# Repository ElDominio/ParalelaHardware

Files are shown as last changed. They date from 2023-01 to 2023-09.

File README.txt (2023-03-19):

4-channel slim ECU with APM32F407VGT6, designed to use RusEFI

4 injection channel
4 ignition channels
additional outputs for boost/fuel pumps/idle/etc
onboard CAN
Hall or external VR conditioner
USB-C connection

No official firmware for this board (for now)

CPU pinout inside "Reference" folder

How to open EasyEDA Project File：

At editor, open the document via: Top menu - File - Open - EasyEDA... , and select the json file, then open it at the editor, you can save it into a project.

如何使用：

打开编辑器，通过：顶部菜单 - 文件 - 打开 - 立创EDA... ，选择 json 文件打开在编辑器，你可以保存文档进工程里面。

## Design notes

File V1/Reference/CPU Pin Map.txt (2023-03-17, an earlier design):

4X4 ECU CPU Pin Map
-------------------

( APM32F407VGT6 )

Ignition 1 >> PA8
Ignition 2 >> PC9
Ignition 3 >> PA10
Ignition 4 >> PC8

Injector 1 >> PE0
Injector 2 >> PE6
Injector 3 >> PA3
Injector 4 >> PA5

IDLE       >> PC5
BOOST      >> PA7
NOS        >> PA6
FAN        >> PC13
FUEL PUMP  >> PC14
TACH       >> PC15

TPS        >> PA0
MAP        >> PA1
CLT        >> PA2
O2         >> PC3
IAT        >> PC2
VBAT       >> PC1

FLEX       >> PE1
CLUTCH     >> PE2

CRANK      >> PE3
CAM        >> PE5

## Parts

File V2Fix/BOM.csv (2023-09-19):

ID | Name | Designator | Footprint | Quantity | Manufacturer Part | Manufacturer | Supplier | Supplier Part | Price
1 | 100nF | C12,C1,C52,C3,C5,C18,C20,C24,C27,C29,C30,C32,C36,C39,C40,C42,C44,C51,C55,C56,C57,C58,C59,C60 | C0402 | 24 | CL05B104KB54PNC | Samsung Electro-Mechanics | LCSC | C307331 | 0.007
2 | 1nF | C34,C35,C14,C16,C17,C22,C23 | C0603 | 7 | CL10B102KB8NNNC | SAMSUNG(三星) | LCSC | C1588 | 0.003
3 | 2.49kΩ | R79 | R1206 | 1 | PTFR1206B2K49P9 | ResistorToday | LCSC | C351475 | 0.222
4 | B340A | D23 | SMA_L4.3-W2.6-LS5.2-RD | 1 | B340A | MDD | LCSC | C64982 | 0.038
5 | 2.4kΩ | R12,R16 | R0402 | 2 | 0402WGF2401TCE | UNI-ROYAL(厚声) | LCSC | C25882 | 0.001
6 | FC-F1005HRK-620H5 | LED1,LED3,LED8,LED9,LED10,LED11 | LED0402-RD | 6 | NCD0402R1 | 国星光电 | LCSC | C130719 | 0.036
7 | SZYY0402B | LED18,LED12,LED13,LED14,LED15 | LED0402-RD_BLUE | 5 | SZYY0402B | yongyu(永裕光电) | LCSC | C434447 | 0.016
8 | 1kΩ | R90,R82,R73,R74,R80,R81,R89 | R0402 | 7 | 0402WGF1001TCE | UNI-ROYAL(厚声) | LCSC | C11702 | 0.001
9 | Header-Male-2.54_2x3 | J1 | HDR-TH_6P-P2.54-V-M-R2-C3-S2.54-1 | 1 | 2.54-2*3P针 | BOOMELE(博穆精密) | LCSC | C65114 | 0.031
10 | 100Ω | L1 | L0805 | 1 | GZ2012D101TF | Sunlord | LCSC | C1015 | 0.009
11 | 10kΩ | RN1 | RES-ARRAY-SMD_0603-8P-L3.2-W1.6-BL | 1 | RC-ML08W103JT | FH | LCSC | C69593 | 0.004
12 | 1uF | C2,C4,C6,C19,C21,C25,C31,C33,C37 | C0402 | 9 | CL05A105KA5NQNC | SAMSUNG | LCSC | C52923 | 0.004
13 | B130-13-F | D1 | SMA_L4.3-W2.6-LS5.2-RD | 1 | B130-13-F | DIODES | LCSC | C134423 | 0.076
14 | SMBJ15CA | D2 | SMB_L4.6-W3.6-LS5.3-BI | 1 | SMBJ15CA | MDD | LCSC | C113989 | 0.046
15 | SMAJ33CA | D3,D4,D5,D11,D12,D13,D14 | SMA_L4.4-W2.6-LS5.0-BI | 7 | SMAJ33CA | MDD | LCSC | C115251 | 0.036
16 | NCE6020AK | Q1,Q6,Q7,Q4,Q5 | TO-252-2_L6.6-W6.1-P4.57-LS10.1-TL-CW | 5 | NCE6020AK | NCE(无锡新洁能) | LCSC | C108639 | 0.136
17 | MCP1416T-E/OT | U4,U5,U6,U8,U9,U13,U14 | SOT-23-5_L3.0-W1.7-P0.95-LS2.8-BL | 7 | MCP1416T-E/OT | MICROCHIP(美国微芯) | LCSC | C83775 | 0.441
18 | USB-TYPE-C-018 | USB1 | USB-C_SMD-TYPE-C-31-M-12 | 1 | USB-TYPE-C-018 | DEALON(德艺隆) | LCSC | C2927038 | 0.052
19 | SZYY0402G | LED16,LED2,LED4,LED5,LED6,LED7 | LED0402-R-RD_GREEN | 6 | SZYY0402G | yongyu(永裕光电) | LCSC | C434446 | 0.016
20 | 100uF | C7 | CAP-SMD_BD6.3-L6.6-W6.6-LS7.4-FD | 1 | RVT100UF35V67RV0034 | KNSCHA(科尼盛) | LCSC | C2836442 | 0.032
21 | 100nF | C8,C9 | C0603 | 2 | CC0603KRX7R9BB104 | YAGEO | LCSC | C14663 | 0.002
22 | 100uF | C10 | CAP-SMD_BD8.0-L8.3-W8.3-RD | 1 | VEJ101M1HTR-0810 | lelon(立隆) | LCSC | C176665 | 0.094
23 | 10uF | C11,C13 | CAP-SMD_L3.2-W1.6-RD-C7171 | 2 | TAJA106K016RNJ | AVX | LCSC | C7171 | 0.094
24 | 1nF | C15,C45,C46,C49,C50 | C0402 | 5 | 0402B102K500NT | FH | LCSC | C1523 | 0.001
25 | 470pF | C47,C48 | C0402 | 2 | 0402B471K500NT | FH | LCSC | C1537 | 0.001
26 | 2.2uF | C53,C64 | C0402 | 2 | CL05A225MQ5NSNC | SAMSUNG | LCSC | C12530 | 0.003
27 | 20pF | C62,C63 | C0402 | 2 | 0402CG200J500NT | FH(风华) | LCSC | C1554 | 0.002
28 | 5557R-2*3P | CN1,CN2 | CONN-TH_5557R-2X3P | 2 | W-5557R06P-0000 | Ckmtw(灿科盟) | LCSC | C124425 | 0.225
29 | 5557R-2*10P | CN3 | CONN-TH_5557R-2-10P | 1 | 5557R-2*10P | Ckmtw | LCSC | C169048 | 0.544
30 | 1N4148WS T4 | D6,D7,D8,D9,D10,D18,D19,D20,D21,D22 | SOD-323_L1.8-W1.3-LS2.5-RD | 10 | 1N4148WS | CJ(江苏长电/长晶) | LCSC | C2128 | 0.01
31 | BAV70 | D15,D16,D17 | SOT-23_L2.9-W1.3-P1.90-LS2.4-BR | 3 | BAV70 | LGE(鲁光) | LCSC | C402233 | 0.014
32 | NCE6005AR | Q2,Q3 | SOT-223_L6.5-W3.5-P2.30-LS7.0-BR | 2 | NCE6005AR | NCE(无锡新洁能) | LCSC | C189606 | 0.172
33 | CJ2310 | Q8,Q9,Q10 | SOT-23-3_L2.9-W1.6-P1.90-LS2.8-BR | 3 | CJ2310 | CJ | LCSC | C75882 | 0.047
34 | 1kΩ | R1 | R1206 | 1 | 1206W4F1001T5E | UNI-ROYAL(厚声) | LCSC | C4410 | 0.003
35 | 27Ω | R2,R6,R7,R25,R27,R47,R49 | R0603 | 7 | 0603WAF270JT5E | UNI-ROYAL(厚声) | LCSC | C25190 | 0.001
36 | 1kΩ | R3,R4,R5,R21,R23,R26,R28,R29,R36,R43,R45,R48,R50,R51,R58,R83 | R0402 | 16 | 0402WGF1001TCE | UniOhm | LCSC | C11702 | 0.001
37 | 10kΩ | R8,R14,R15,R31,R33,R53,R55 | R0603 | 7 | 0603WAF1002T5E | UNI-ROYAL(厚声) | LCSC | C25804 | 0.001
38 | 10kΩ | R9,R10,R11,R22,R32,R34,R35,R44,R54,R56,R57,R66,R85,R86 | R0402 | 14 | 0402WGF1002TCE | UniOhm | LCSC | C25744 | 0.001
39 | 1.5kΩ | R13,R17,R18,R19,R20,R62,R63,R64,R65,R77 | R0402 | 10 | 0402WGF1501TCE | UNI-ROYAL(厚声) | LCSC | C25867 | 0.001
40 | 10Ω | R24,R30,R46,R52 | R1206 | 4 | AS0606J0100T5E | UNI-ROYAL(Uniroyal Elec) | LCSC | C966096 | 0.032
41 | 10kΩ | R37,R38,R39,R40,R59,R60,R68,R69,R75,R76 | R0402 | 10 | AR02BTC1002 | Viking Tech | LCSC | C317926 | 0.03
42 | 20kΩ | R41,R42,R61,R71,R78 | R0603 | 5 | AR03BTCX2002 | Viking(光颉) | LCSC | C319766 | 0.032
43 | 2.7kΩ | R67,R72 | R0603 | 2 | RT0603BRD072K7L | YAGEO(国巨) | LCSC | C705760 | 0.026
44 | 120Ω | R70 | R0805 | 1 | 0805W8F1200T5E | UniOhm | LCSC | C17437 | 0.002
45 | 100Ω | R84 | R0402 | 1 | 0402WGF1000TCE | UNI-ROYAL(厚声) | LCSC | C25076 | 0.001
46 | L78M05CDT-TR | U1 | TO-252-3_L6.5-W5.8-P4.58-BL | 1 | L78M05CDT-TR | ST(意法半导体) | LCSC | C55509 | 0.155
47 | SPX3819M5-L-3-3/TR | U2 | SOT-23-5_L3.0-W1.7-P0.95-LS2.8-BR | 1 | SPX3819M5-L-3-3/TR | EXAR | LCSC | C9055 | 0.149
48 | ULN2001D | U3 | SOP-8_L4.9-W3.9-P1.27-LS6.0-TL | 1 | ULN2001D | LANKE(兰科) | LCSC | C2828554 | 0.075
49 | TC4424AVOA713 | U7,U12 | SOIC-8_L4.9-W3.9-P1.27-LS6.0-BL | 2 | TC4424AVOA713 | MICROCHIP(美国微芯) | LCSC | C44150 | 0.767
50 | MCP6004T-I/ST | U10 | TSSOP-14_L5.0-W4.4-P0.65-LS6.4-BL | 1 | MCP6004T-I/ST | MICROCHIP(美国微芯) | LCSC | C50282 | 0.638
51 | MCP6001T-I/OT | U11 | SOT-23-5_L3.0-W1.7-P0.95-LS2.8-BR | 1 | MCP6001T-I/OT | MICROCHIP(美国微芯) | LCSC | C116490 | 0.289
52 | SN65HVD230DR | U15 | SOIC-8_L4.9-W3.9-P1.27-LS6.0-BL | 1 | SN65HVD230DR | TI | LCSC | C12084 | 0.959
53 | 8 MHz | X1 | OSC-SMD_L5.0-W3.2 | 1 | NX5032GA-8MHZ(STD-CSK-7) | Nihon Dempa Kogyo | LCSC | C156253 | 0.273
54 | 1uF | C65 | C0805 | 1 | CL21B105KBFNNNE | SAMSUNG(三星) | LCSC | C28323 | 0.009
55 | 10kΩ | R87 | R0805 | 1 | ARG05BTC1002 | Viking(光颉) | LCSC | C406725 | 0.025
56 | 82kΩ | R88 | R0805 | 1 | PTFR0805B82K0N9 | RESI(开步睿思） | LCSC | C351545 | 0.151
57 | SRV05-4-P-T7 | TV2 | SOT-23-6_L2.9-W1.6-P0.95-LS2.8-BR | 1 | SRV05-4-P-T7 | PROTEK | LCSC | C85364 | 0.176
58 | APM32F407VGT6 | U16 | LQFP-100_L14.0-W14.0-P0.50-LS16.0-BL | 1 | APM32F407VGT6 | Geehy(珠海极海) | LCSC | C2990873 | 4.434
59 | TZ-P2-0402GTIA1-0.45T | LED17 | LED0402-RD | 1 | TZ-P2-0402GTIA1-0.45T | TUOZHAN(拓展光电) | LCSC | C688877 | 0.011

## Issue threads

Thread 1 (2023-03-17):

separate versioned output from sources

rusefillc, 2023-03-17:
current file structure is a naive mess

please be like proteus - explicit separate folder for each revision of outputs like https://github.com/mck1117/proteus/tree/master/export

ElDominio, 2023-03-19:
Solved by 720e451

Closed 2023-03-19.

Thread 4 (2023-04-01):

programming header: reset less important than GND

rusefillc, 2023-04-01:
if you have only three pins GND should be one of those. Reset is kind of optional less imporant

ElDominio, 2023-04-16:
Fixed by b19c86d

Closed 2023-04-16.

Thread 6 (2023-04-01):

arm chip should be powered by USB

rusefillc, 2023-04-01:
if you hook USB you should have 3.3 on the chip and happy chip right?

ElDominio, 2023-04-02:
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

Adding a solder bridge here produces a chip that is happy to wake on USB connection

ElDominio, 2023-04-16:
Fixed by b19c86d

Closed 2023-04-16.

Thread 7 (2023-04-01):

LEDs are WAY too bright, use other color

ElDominio, 2023-04-01:
5v and 12v LEDs are incredibly bright

ElDominio, 2023-04-16:
Fixed by b19c86d

Closed 2023-04-16.

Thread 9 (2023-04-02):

c'mon no blue LED to show life?

rusefillc, 2023-04-02:
Please consider a blue "firmware is alive" LED

ElDominio, 2023-04-02:
to what pin does it get connected to?

ElDominio, 2023-04-16:
Fixed by b19c86d

Closed 2023-04-16.

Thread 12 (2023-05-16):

PC14 does not work, all other outputs do

ElDominio, 2023-05-16:
As stated, PC14 seems to do nothing. Is this pin different on APM32?

rusefillc, 2023-05-16:
"google PC14 stm32" to see if that's one of the special magic pins

looks like it's a pin for low speed oscillator?

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

This indicates that custom binary would be needed which is major effort. Would it be possible to adjust hardware and use a less magical stm32 pin?

ElDominio, 2023-09-19:
Changed pin

Closed 2023-09-19.

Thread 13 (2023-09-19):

only Some APM32 Paralelas report "Device Descriptor Request Failed" on USB, processor seems alive?

ElDominio, 2023-09-19:
Some Paralelas after flashing f407-discovery seem to have USB comms die, but still talk fine with STLink, and flash leds as if everything is ok. Satanic possesion? Probably due to Geehy not being STM and incompatibilities from this

rusefillc, 2023-09-25:
https://github.com/ElDominio/ParalelaHardware/blob/main/V2Fix/Schematic.pdf

ElDominio, 2023-09-30:
Most of them flash fine, connect to tunerstudio, and after you disconnect and reconnect they never come back to life through usb, even though processor seems to be alive and well

rusefillc, 2023-10-07:
@ElDominio what oscillator frequency is mounter? 8mhz? 12mhz? else?

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

rusefillc, 2023-10-07:
```"8 MHz"	"X1"	"OSC-SMD_L5.0-W3.2"	"1"	"NX5032GA-8MHZ(STD-CSK-7)"	"Nihon Dempa Kogyo"```

ElDominio, 2023-10-07:
Where is that? in STM32cube? Or in Device Manager?

rusefillc, 2023-10-07:
> Where is that? in STM32cube? Or in Device Manager? I don't even know what a "mounter" is

that's eclipse debugging session

ElDominio, 2023-10-07:
> Most of them flash fine, connect to tunerstudio, and after you disconnect and reconnect they never come back to life through usb, even though processor seems to be alive and well

Just quoting this because of oddness.
USB comms dies, but everything else is still alive, you can flash firmware as many times as you want but it will still be broken

ElDominio, 2023-10-17:
@rusefillc not due to processor, same happens on OG STM32 boards. Still alive through DFU

ElDominio, 2023-10-17:
weirder: they started talking through USB again? with no intervention from my part?

rusefillc, 2023-10-17:
smells like firmware issue

ElDominio, 2023-10-19:
Another fun fact:

I got another batch of STM32 Paralelas, have only tested 3 but I have loaded firmware+tune and they all seem alive and well, even with multiple USB connect/disconnects. This is pointing more to a specific hardware+firmware issue concerning APM32. Will have more tests coming in the coming weeks.

@rusefillc  you need 3 STM, and you will ship 1x APM + 1 STM Paralela to Ukraine correct?

rusefillc, 2023-10-19:
@ElDominio I am mostly interested in BROKEN stm32

please do NOT ship any stm32 of the "good" batch

ElDominio, 2023-10-19:
At the current time, ALL STM32 Paralelas are working fine. Two had a hiccup yesterday but seem to be back to life with no further errors. Next one that locks up I will put in a box for @rusefillc

ElDominio, 2023-10-29:
This seems to be very APM-specific. Up until now _ALL_ STM32's have not suffered this for more than one or two restarts, after which it does not come back.

ElDominio, 2024-02-23:
This is due to using APM32 chips. Zero STM chips have had this issue. If not useful, will close

ElDominio, 2024-04-06:
Not useful, will close

Closed 2024-04-06.

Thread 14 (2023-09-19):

Paralela magic smoke report

ElDominio, 2023-09-19:
Users were working on alternator with engine on, seem to have overvolted by a large degree resulting in D2 diode exploding

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

ElDominio, 2023-10-29:
Owner used battery booster in engine start and fed >16v. Diode was overvolt protection diode, replaced diode and is still alive

Closed 2023-10-29.

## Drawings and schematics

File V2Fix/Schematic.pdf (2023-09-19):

A | A

1

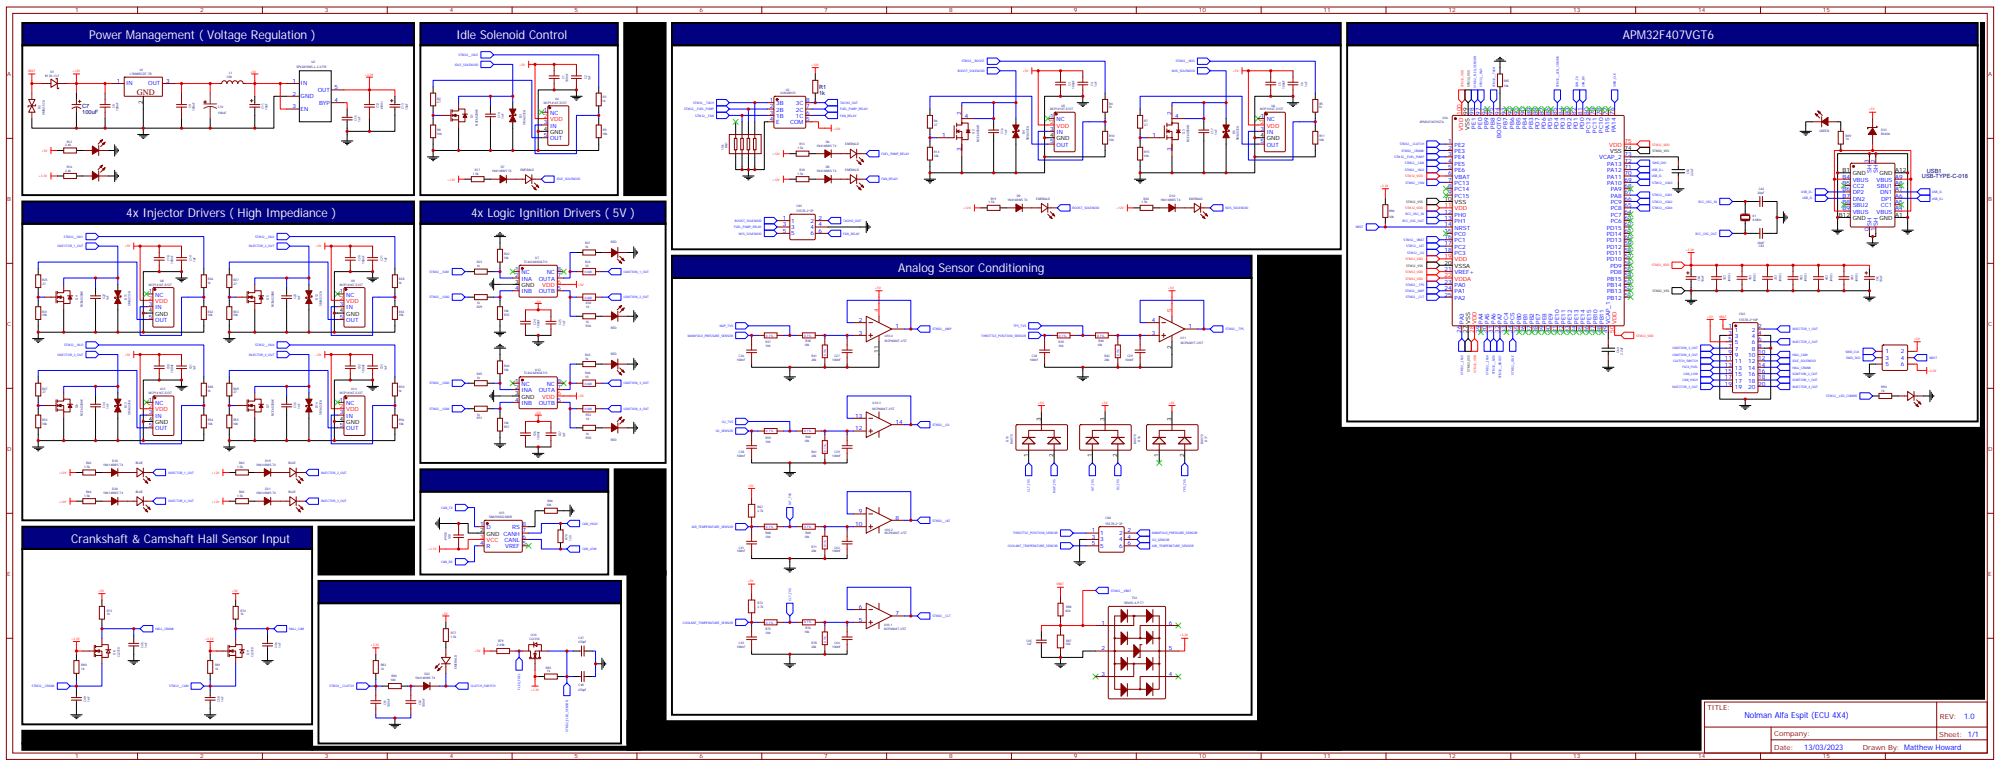
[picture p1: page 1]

Power Management ( Voltage Regulation )

4x Injector Drivers ( High Impediance )

Drawn By: Matthew Howard

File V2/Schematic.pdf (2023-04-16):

A | A

1

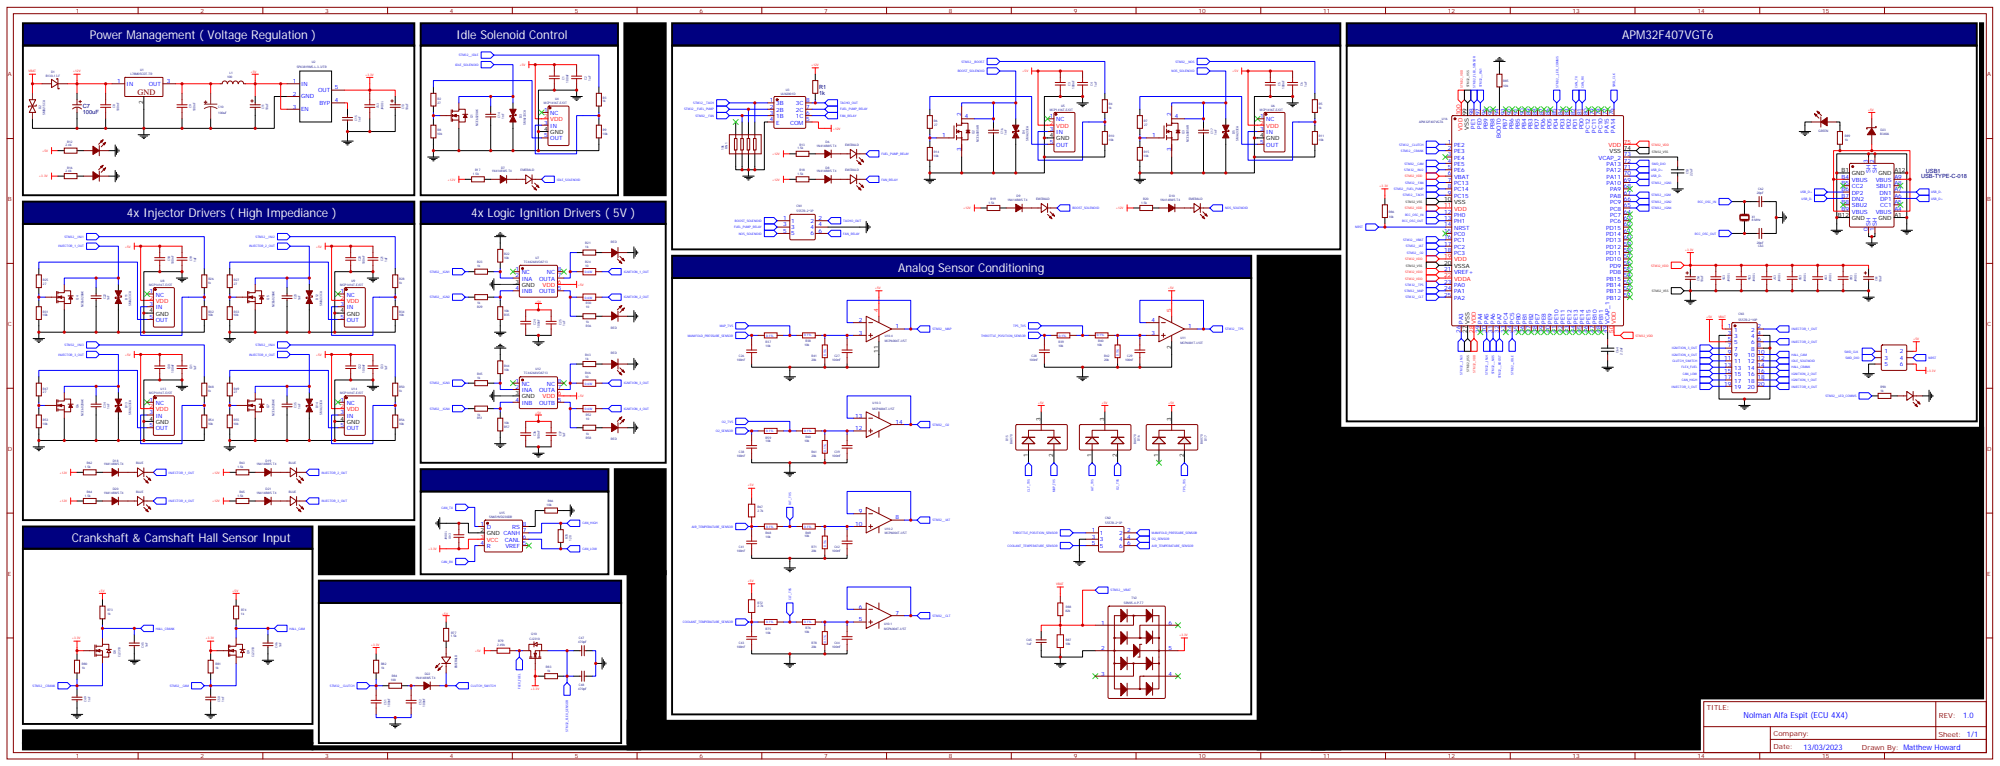
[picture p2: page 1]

Power Management ( Voltage Regulation )

4x Injector Drivers ( High Impediance )

Drawn By: Matthew Howard

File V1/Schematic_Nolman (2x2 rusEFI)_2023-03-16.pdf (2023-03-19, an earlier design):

A | A

1

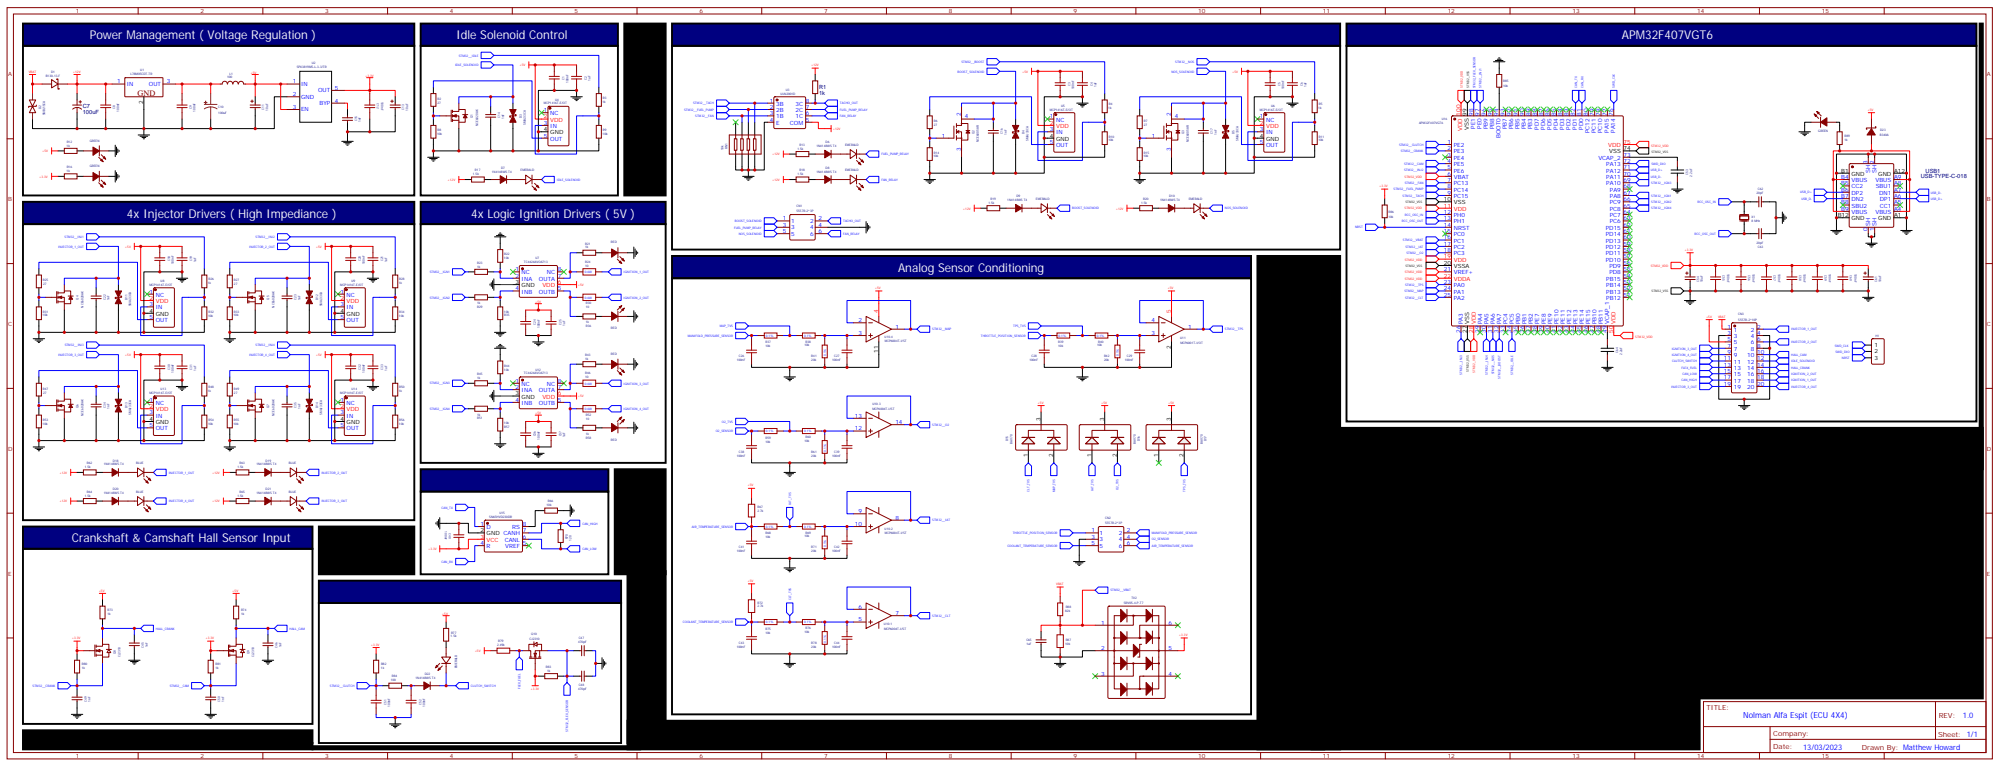
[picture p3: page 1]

Power Management ( Voltage Regulation )

4x Injector Drivers ( High Impediance )

Drawn By: Matthew Howard

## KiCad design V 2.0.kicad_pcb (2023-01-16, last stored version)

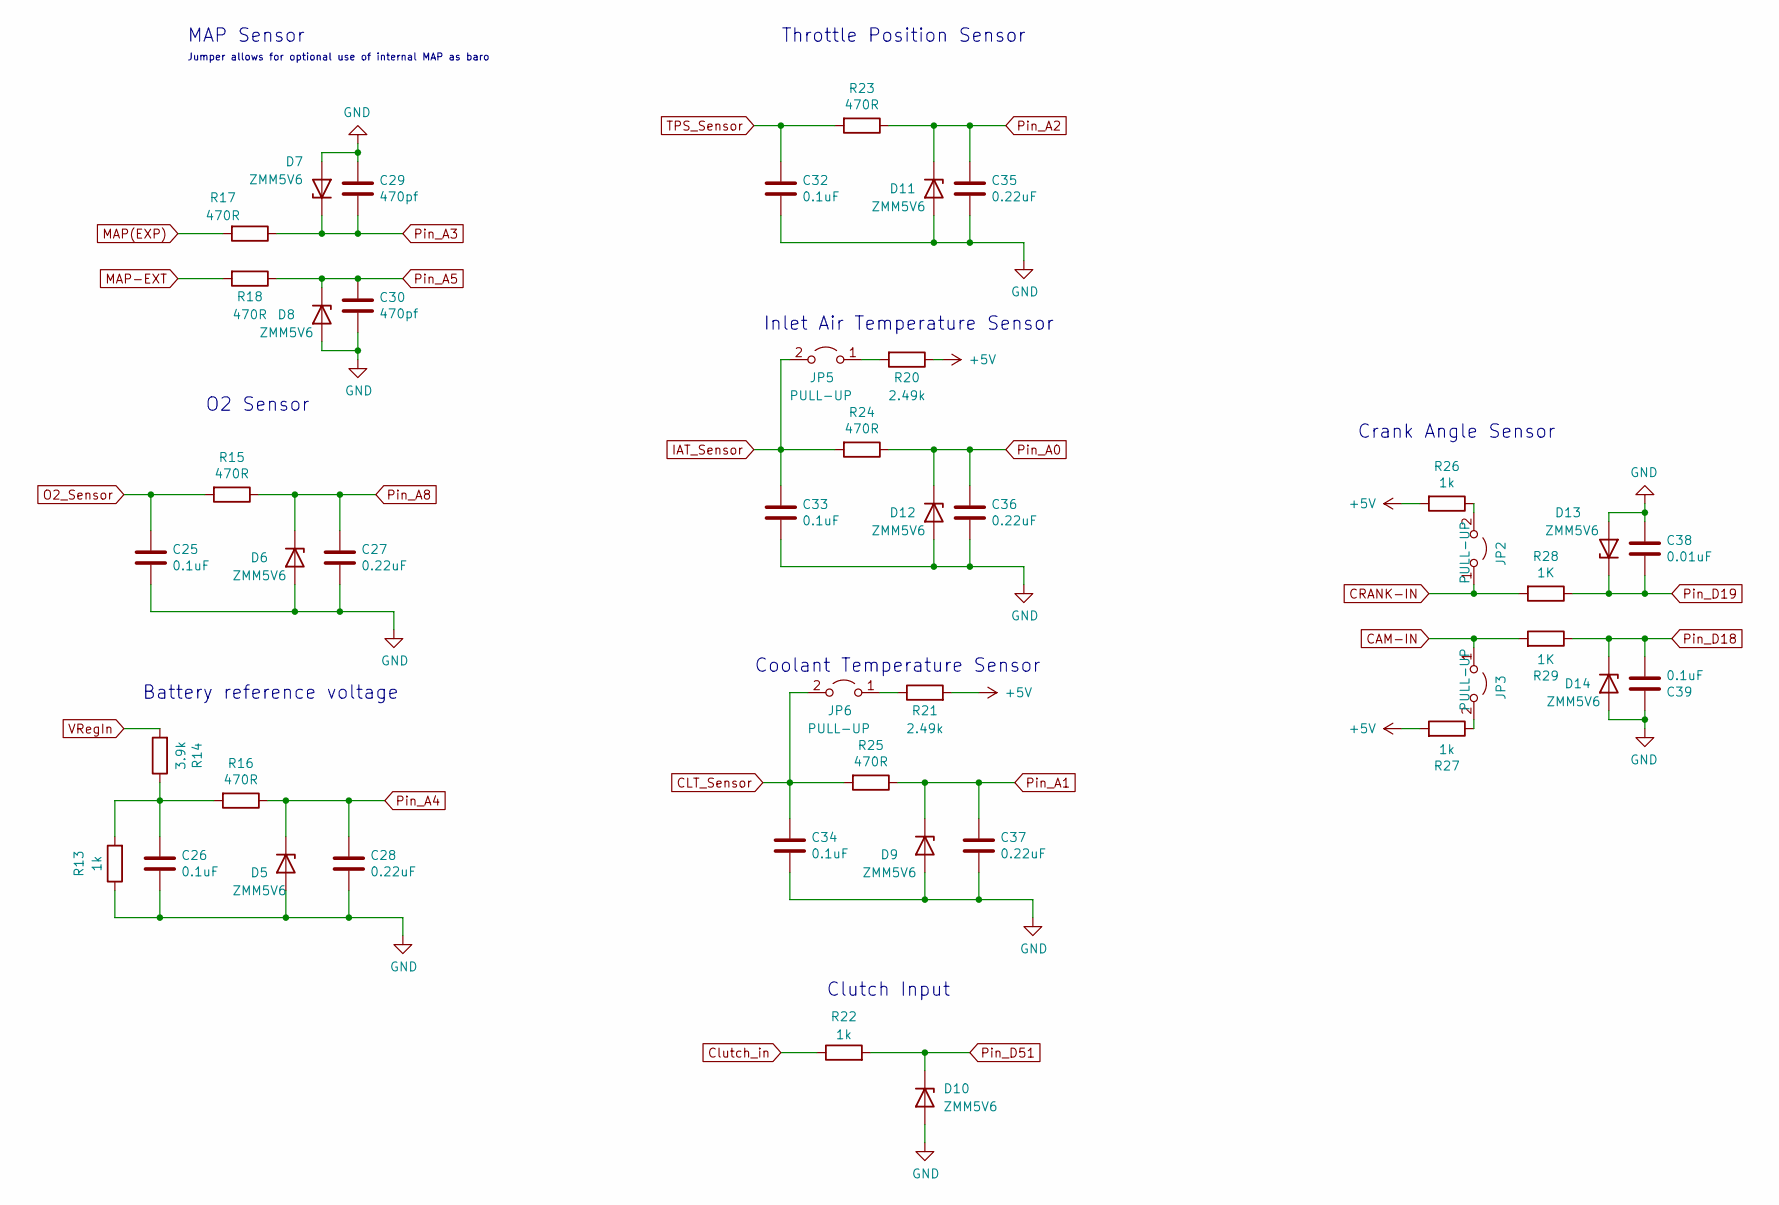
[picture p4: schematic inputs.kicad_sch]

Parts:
C25, C26, C32, C33, C34, C39: 0.1uF; C_0805_2012Metric; LCSC Part Number C49678
C27, C28, C35, C36, C37: 0.22uF; C_0805_2012Metric
C29, C30: 470pf; C_0805_2012Metric; LCSC Part Number C76630
C38: 0.01uF; C_0805_2012Metric
D5, D6, D7, D8, D9, D10, D11, D12, D13, D14: ZMM5V6; D_SOD-123; LCSC Part Number C8062
JP2, JP3: PULL-UP; PinHeader_1x02_P2.54mm_Vertical; LCSC Part Number C5116481
JP5, JP6: PULL-UP; SolderJumper-2_P1.3mm_Open_Pad1.0x1.5mm
R13, R22, R26, R27: 1k; R_0805_2012Metric; LCSC Part Number C408924
R14: 3.9k; R_0805_2012Metric; LCSC Part Number C171021
R15, R16, R17, R18, R23, R24, R25: 470R; R_0805_2012Metric; LCSC Part Number C229215
R20, R21: 2.49k; R_0805_2012Metric; LCSC Part Number C325835
R28, R29: 1K; R_0805_2012Metric; LCSC Part Number C416075

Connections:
+5V: R20.1, R21.2, R26.2, R27.2; also elsewhere on the board
CAM-IN: JP3.1 (A), R29.2; also elsewhere on the board
CLT_Sensor: C34.1, JP6.2 (B), R25.2; also elsewhere on the board
CRANK-IN: JP2.1 (A), R28.2; also elsewhere on the board
Clutch_in: R22.1; also elsewhere on the board
GND: C25.2, C26.2, C27.2, C28.2, C29.1, C30.2, C32.2, C33.2, C34.2, C35.2, C36.2, C37.2, C38.1, C39.1, D5.2 (A), D6.2 (A), D7.2 (A), D8.2 (A), D9.2 (A), D10.2 (A), D11.2 (A), D12.2 (A), D13.2 (A), D14.2 (A), R13.1; also elsewhere on the board
IAT_Sensor: C33.1, JP5.2 (B), R24.2; also elsewhere on the board
MAP(EXP): R17.2; also elsewhere on the board
MAP-EXT: R18.2; also elsewhere on the board
unnamed: C26.1, R13.2, R14.1, R16.2
unnamed: JP2.2 (B), R26.1
unnamed: JP3.2 (B), R27.1
unnamed: JP5.1 (A), R20.2
unnamed: JP6.1 (A), R21.1
O2_Sensor: C25.1, R15.2; also elsewhere on the board
Pin_A0: C36.1, D12.1 (K), R24.1; also elsewhere on the board
Pin_A1: C37.1, D9.1 (K), R25.1; also elsewhere on the board
Pin_A2: C35.1, D11.1 (K), R23.1; also elsewhere on the board
Pin_A3: C29.2, D7.1 (K), R17.1; also elsewhere on the board
Pin_A4: C28.1, D5.1 (K), R16.1; also elsewhere on the board
Pin_A5: C30.1, D8.1 (K), R18.1; also elsewhere on the board
Pin_A8: C27.1, D6.1 (K), R15.1; also elsewhere on the board
Pin_D18: C39.2, D14.1 (K), R29.1; also elsewhere on the board
Pin_D19: C38.2, D13.1 (K), R28.1; also elsewhere on the board
Pin_D51: D10.1 (K), R22.2; also elsewhere on the board
TPS_Sensor: C32.1, R23.2; also elsewhere on the board
VRegIn: R14.2; also elsewhere on the board

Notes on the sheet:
Coolant Temperature Sensor
Throttle Position Sensor
O2 Sensor
Inlet Air Temperature Sensor
Clutch Input
Battery reference voltage
Jumper allows for optional use of internal MAP as baro
MAP Sensor
Crank Angle Sensor

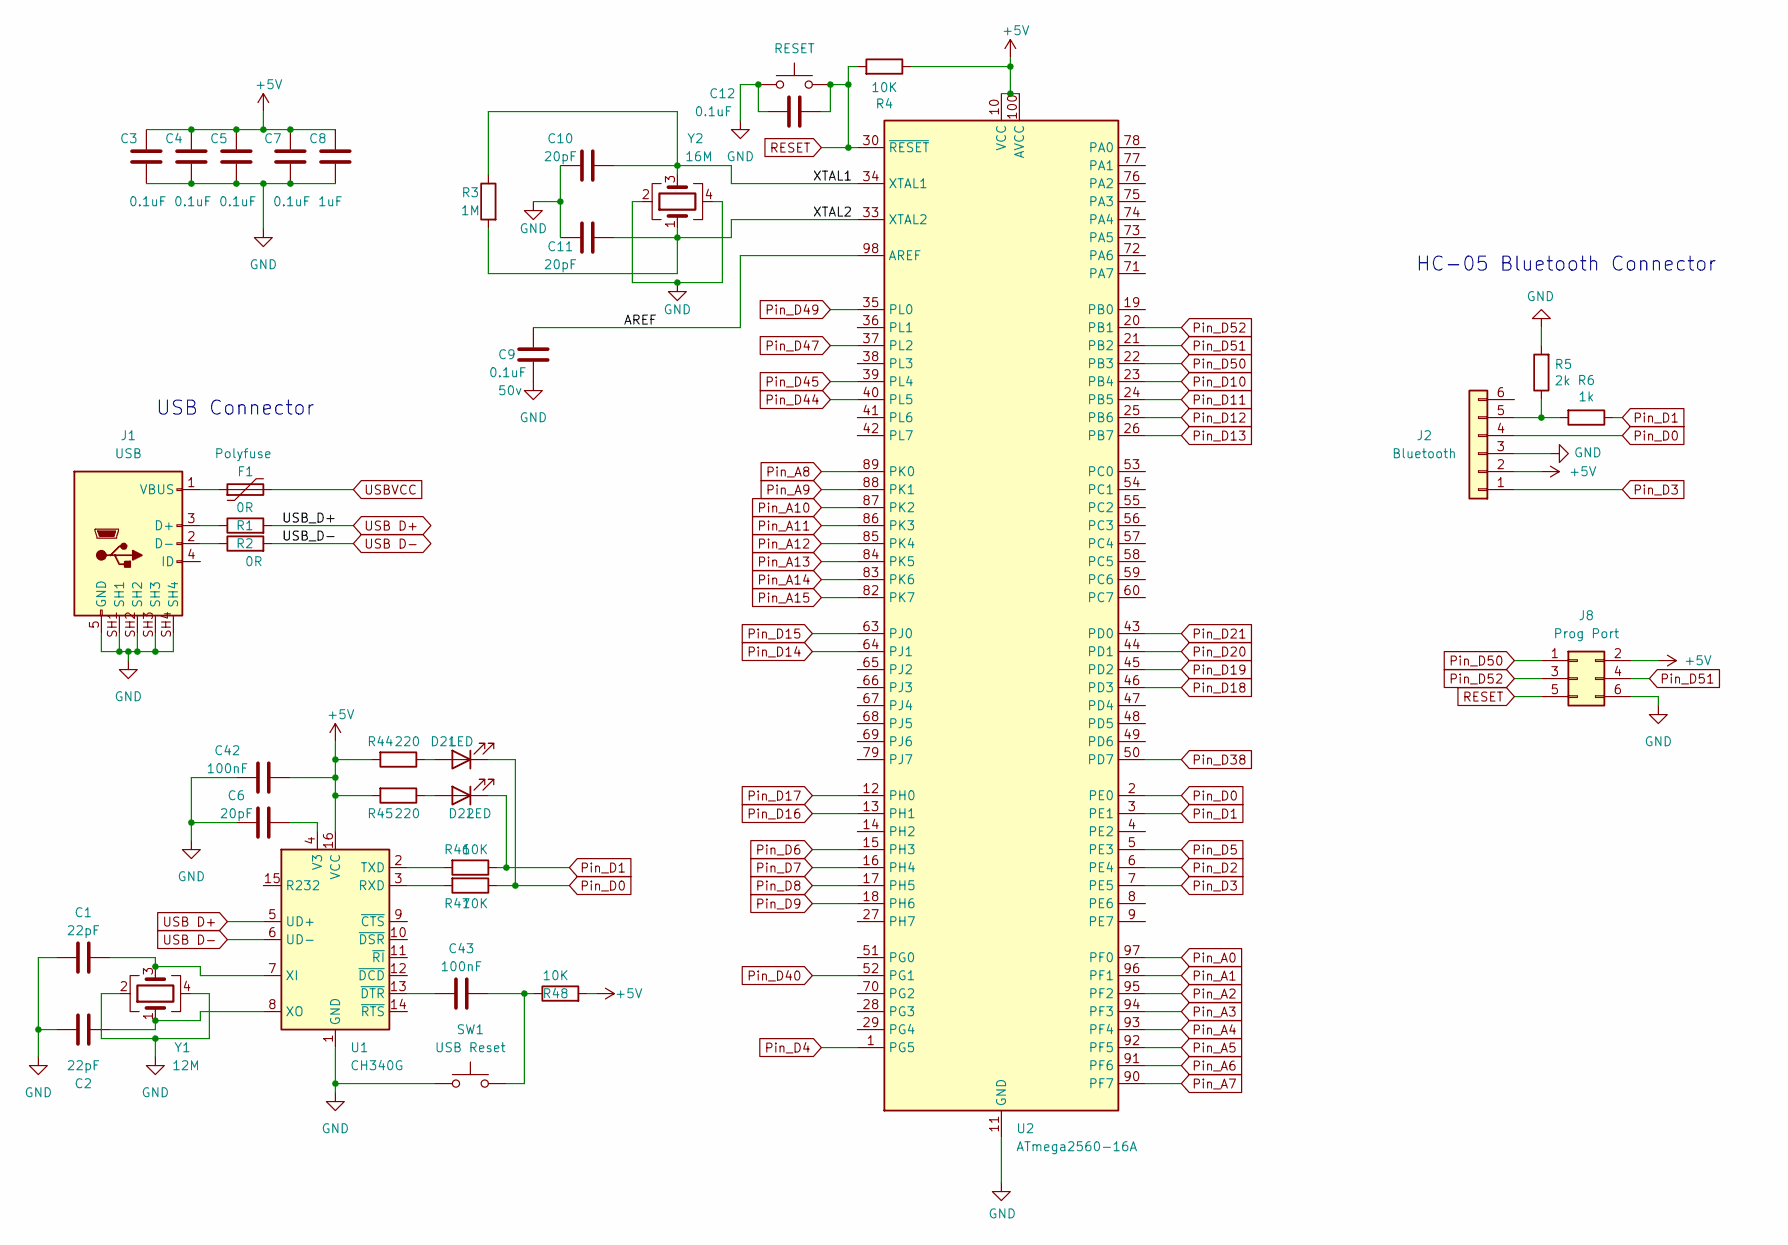
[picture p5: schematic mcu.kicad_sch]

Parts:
C1, C2: 22pF; C_0805_2012Metric; LCSC Part Number C149614
C3, C4, C5, C7, C12: 0.1uF; C_0805_2012Metric; LCSC Part Number C49678
C6, C10, C11: 20pF; C_0805_2012Metric; LCSC Part Number C149606
C8: 1uF; C_0805_2012Metric; LCSC Part Number C105952
C9: 0.1uF; C_0805_2012Metric; Voltage 50v; LCSC Part Number C49678
C42, C43: 100nF; C_0805_2012Metric; LCSC Part Number C495959
D21, D22: LED; LED_0805_2012Metric; LCSC Part Number C84256
F1: Polyfuse; Fuse_1812_4532Metric
J1: USB; USB Connector; LCSC Part Number C69074
J2: Bluetooth; PinHeader_1x06_P2.54mm_Vertical; LCSC Part Number C5156615
J8: Prog Port; PinHeader_2x03_P2.54mm_Vertical; LCSC Part Number C65114
R1, R2: 0R; R_0805_2012Metric; LCSC Part Number C728266
R3: 1M; R_0805_2012Metric; LCSC Part Number C416080
R4, R46, R47, R48: 10K; R_0805_2012Metric; LCSC Part Number C416062
R5: 2k; R_0805_2012Metric; LCSC Part Number C285226
R6: 1k; R_0805_2012Metric; LCSC Part Number C408924
R44, R45: 220; R_0805_2012Metric; LCSC Part Number C114519
RESET1: RESET; SW_Push_SPST_NO_Alps_SKRK
SW1: USB Reset; SW_Push_SPST_NO_Alps_SKRK
U1: CH340G; SOIC-16_3.9x9.9mm_P1.27mm; LCSC Part Number C14267
U2: ATmega2560-16A; TQFP-100_14x14mm_P0.5mm; LCSC Part Number C22460
Y1: 12M; Crystal_SMD_3225-4Pin_3.2x2.5mm; LCSC Part Number C9002
Y2: 16M; Crystal_SMD_3225-4Pin_3.2x2.5mm; LCSC Part Number C13738

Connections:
+5V: C3.2, C4.2, C5.2, C7.2, C8.2, C42.2, J2.2, J8.2, R4.1, R44.2, R45.2, R48.2, U1.16 (VCC), U2.10 (VCC), U2.31 (VCC), U2.61 (VCC), U2.80 (VCC), U2.100 (AVCC); also elsewhere on the board
/MCU/AREF: C9.1, U2.98 (AREF)
/MCU/XTAL1: C10.2, R3.1, U2.34 (XTAL1), Y2.3
/MCU/XTAL2: C11.2, R3.2, U2.33 (XTAL2), Y2.1
GND: C1.1, C2.1, C3.1, C4.1, C5.1, C6.1, C7.1, C8.1, C9.2, C10.1, C11.1, C12.2, C42.1, J1.5 (GND), J1.SH1, J1.SH2, J1.SH3, J1.SH4, J2.3, J8.6, R5.2, RESET1.1, SW1.1, U1.1 (GND), U2.11 (GND), U2.32 (GND), U2.62 (GND), U2.81 (GND), U2.99 (GND), Y1.2, Y1.4, Y2.2, Y2.4; also elsewhere on the board
unnamed: C1.2, U1.7 (XI), Y1.3
unnamed: C2.2, U1.8 (XO), Y1.1
unnamed: C6.2, U1.4 (V3)
unnamed: C43.1, U1.13 (~DTR)
unnamed: C43.2, R48.1, SW1.2
unnamed: D21.2 (A), R44.1
unnamed: D22.2 (A), R45.1
unnamed: F1.1, J1.1 (VBUS)
unnamed: J1.2 (D-), R2.1
unnamed: J1.3 (D+), R1.1
unnamed: J2.5, R5.1, R6.2
unnamed: R46.2, U1.2 (TXD)
unnamed: R47.2, U1.3 (RXD)
Pin_A0: U2.97 (PF0); also elsewhere on the board
Pin_A1: U2.96 (PF1); also elsewhere on the board
Pin_A2: U2.95 (PF2); also elsewhere on the board
Pin_A3: U2.94 (PF3); also elsewhere on the board
Pin_A4: U2.93 (PF4); also elsewhere on the board
Pin_A5: U2.92 (PF5); also elsewhere on the board
Pin_A6: U2.91 (PF6)
Pin_A7: U2.90 (PF7)
Pin_A8: U2.89 (PK0); also elsewhere on the board
Pin_A9: U2.88 (PK1); also elsewhere on the board
Pin_A10: U2.87 (PK2); also elsewhere on the board
Pin_A11: U2.86 (PK3)
Pin_A12: U2.85 (PK4)
Pin_A13: U2.84 (PK5)
Pin_A14: U2.83 (PK6)
Pin_A15: U2.82 (PK7)
Pin_D0: D21.1 (K), J2.4, R47.1, U2.2 (PE0)
Pin_D1: D22.1 (K), R6.1, R46.1, U2.3 (PE1)
Pin_D2: U2.6 (PE4); also elsewhere on the board
Pin_D3: J2.1, U2.7 (PE5)
Pin_D4: U2.1 (PG5); also elsewhere on the board
Pin_D5: U2.5 (PE3); also elsewhere on the board
Pin_D6: U2.15 (PH3); also elsewhere on the board
Pin_D7: U2.16 (PH4); also elsewhere on the board
Pin_D8: U2.17 (PH5); also elsewhere on the board
Pin_D9: U2.18 (PH6); also elsewhere on the board
Pin_D10: U2.23 (PB4); also elsewhere on the board
Pin_D11: U2.24 (PB5); also elsewhere on the board
Pin_D12: U2.25 (PB6)
Pin_D13: U2.26 (PB7)
Pin_D14: U2.64 (PJ1); also elsewhere on the board
Pin_D15: U2.63 (PJ0); also elsewhere on the board
Pin_D16: U2.13 (PH1)
Pin_D17: U2.12 (PH0)
Pin_D18: U2.46 (PD3); also elsewhere on the board
Pin_D19: U2.45 (PD2); also elsewhere on the board
Pin_D20: U2.44 (PD1); also elsewhere on the board
Pin_D21: U2.43 (PD0)
Pin_D38: U2.50 (PD7); also elsewhere on the board
Pin_D40: U2.52 (PG1); also elsewhere on the board
Pin_D44: U2.40 (PL5); also elsewhere on the board
Pin_D45: U2.39 (PL4); also elsewhere on the board
Pin_D47: U2.37 (PL2); also elsewhere on the board
Pin_D49: U2.35 (PL0); also elsewhere on the board
Pin_D50: J8.1, U2.22 (PB3); also elsewhere on the board
Pin_D51: J8.4, U2.21 (PB2); also elsewhere on the board
Pin_D52: J8.3, U2.20 (PB1); also elsewhere on the board
RESET: C12.1, J8.5, R4.2, RESET1.2, U2.30 (~RESET); also elsewhere on the board
USB D+: R1.2, U1.5 (UD+)
USB D-: R2.2, U1.6 (UD-)
USBVCC: F1.2; also elsewhere on the board

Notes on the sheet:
HC-05 Bluetooth Connector
USB Connector

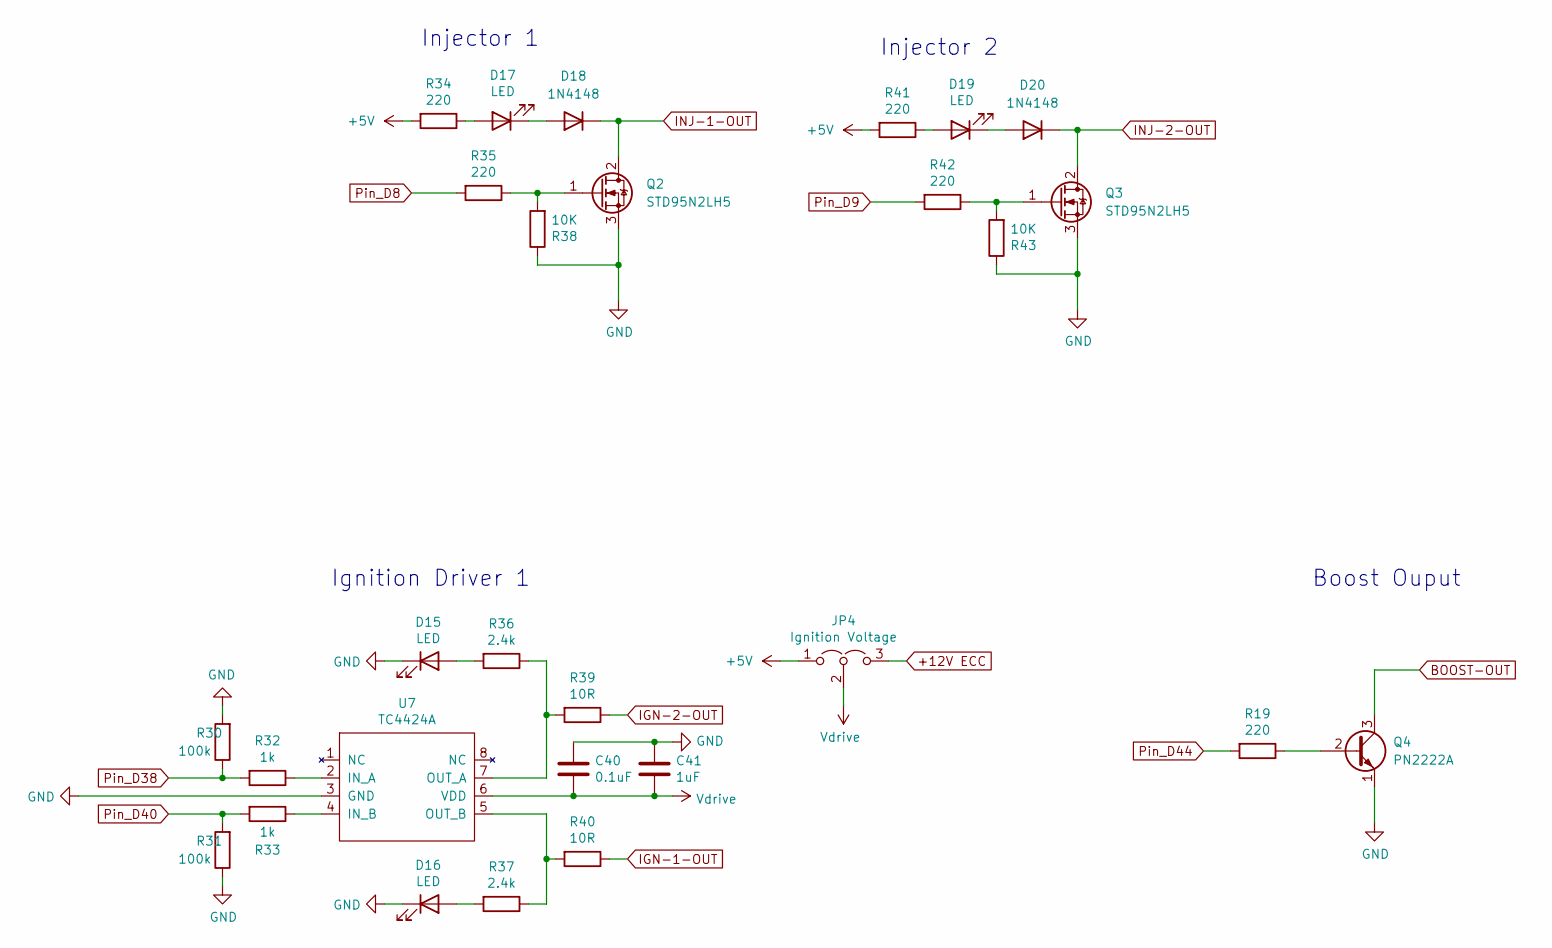
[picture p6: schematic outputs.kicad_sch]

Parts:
C40: 0.1uF; C_0805_2012Metric; LCSC Part Number C49678
C41: 1uF; C_0805_2012Metric; LCSC Part Number C105952
D15, D16, D17, D19: LED; LED_0805_2012Metric; LCSC Part Number C84256
D18, D20: 1N4148; D_0805_2012Metric_Pad1.15x1.40mm_HandSolder
JP4: Ignition Voltage; PinHeader_1x03_P2.54mm_Vertical; LCSC Part Number C306127
Q2, Q3: STD95N2LH5; TO-252-3_TabPin2; LCSC Part Number C155647
Q4: PN2222A; SOT-23; LCSC Part Number C80781
R19, R34, R35, R41, R42: 220; R_0805_2012Metric; LCSC Part Number C114519
R30, R31: 100k; R_0805_2012Metric; LCSC Part Number C416061
R32, R33: 1k; R_0805_2012Metric; LCSC Part Number C408924
R36, R37: 2.4k; R_0805_2012Metric; LCSC Part Number C325803
R38, R43: 10K; R_0805_2012Metric; LCSC Part Number C416062
R39, R40: 10R; R_0805_2012Metric; LCSC Part Number C212287
U7: TC4424A; SOIC-8_3.9x4.9mm_P1.27mm; LCSC Part Number C44150

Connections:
+5V: JP4.1 (A), R34.2, R41.2; also elsewhere on the board
+12V ECC: JP4.3 (B)
BOOST-OUT: Q4.3 (C); also elsewhere on the board
GND: C40.1, C41.1, D15.1 (K), D16.1 (K), Q2.3 (S), Q3.3 (S), Q4.1 (E), R30.2, R31.1, R38.1, R43.1, U7.3 (GND); also elsewhere on the board
IGN-1-OUT: R40.1; also elsewhere on the board
IGN-2-OUT: R39.1; also elsewhere on the board
INJ-1-OUT: D18.1 (K), Q2.2 (D); also elsewhere on the board
INJ-2-OUT: D20.1 (K), Q3.2 (D); also elsewhere on the board
unnamed: D15.2 (A), R36.2
unnamed: D16.2 (A), R37.2
unnamed: D17.1 (K), D18.2 (A)
unnamed: D17.2 (A), R34.1
unnamed: D19.1 (K), D20.2 (A)
unnamed: D19.2 (A), R41.1
unnamed: Q2.1 (G), R35.1, R38.2
unnamed: Q3.1 (G), R42.1, R43.2
unnamed: Q4.2 (B), R19.1
unnamed: R32.1, U7.2 (IN_A)
unnamed: R33.1, U7.4 (IN_B)
unnamed: R36.1, R39.2, U7.7 (OUT_A)
unnamed: R37.1, R40.2, U7.5 (OUT_B)
Pin_D8: R35.2; also elsewhere on the board
Pin_D9: R42.2; also elsewhere on the board
Pin_D38: R30.1, R32.2; also elsewhere on the board
Pin_D40: R31.2, R33.2; also elsewhere on the board
Pin_D44: R19.2; also elsewhere on the board
Vdrive: C40.2, C41.2, JP4.2 (C), U7.6 (VDD)

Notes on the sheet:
Ignition Driver 1
Boost Ouput
Injector 1
Injector 2

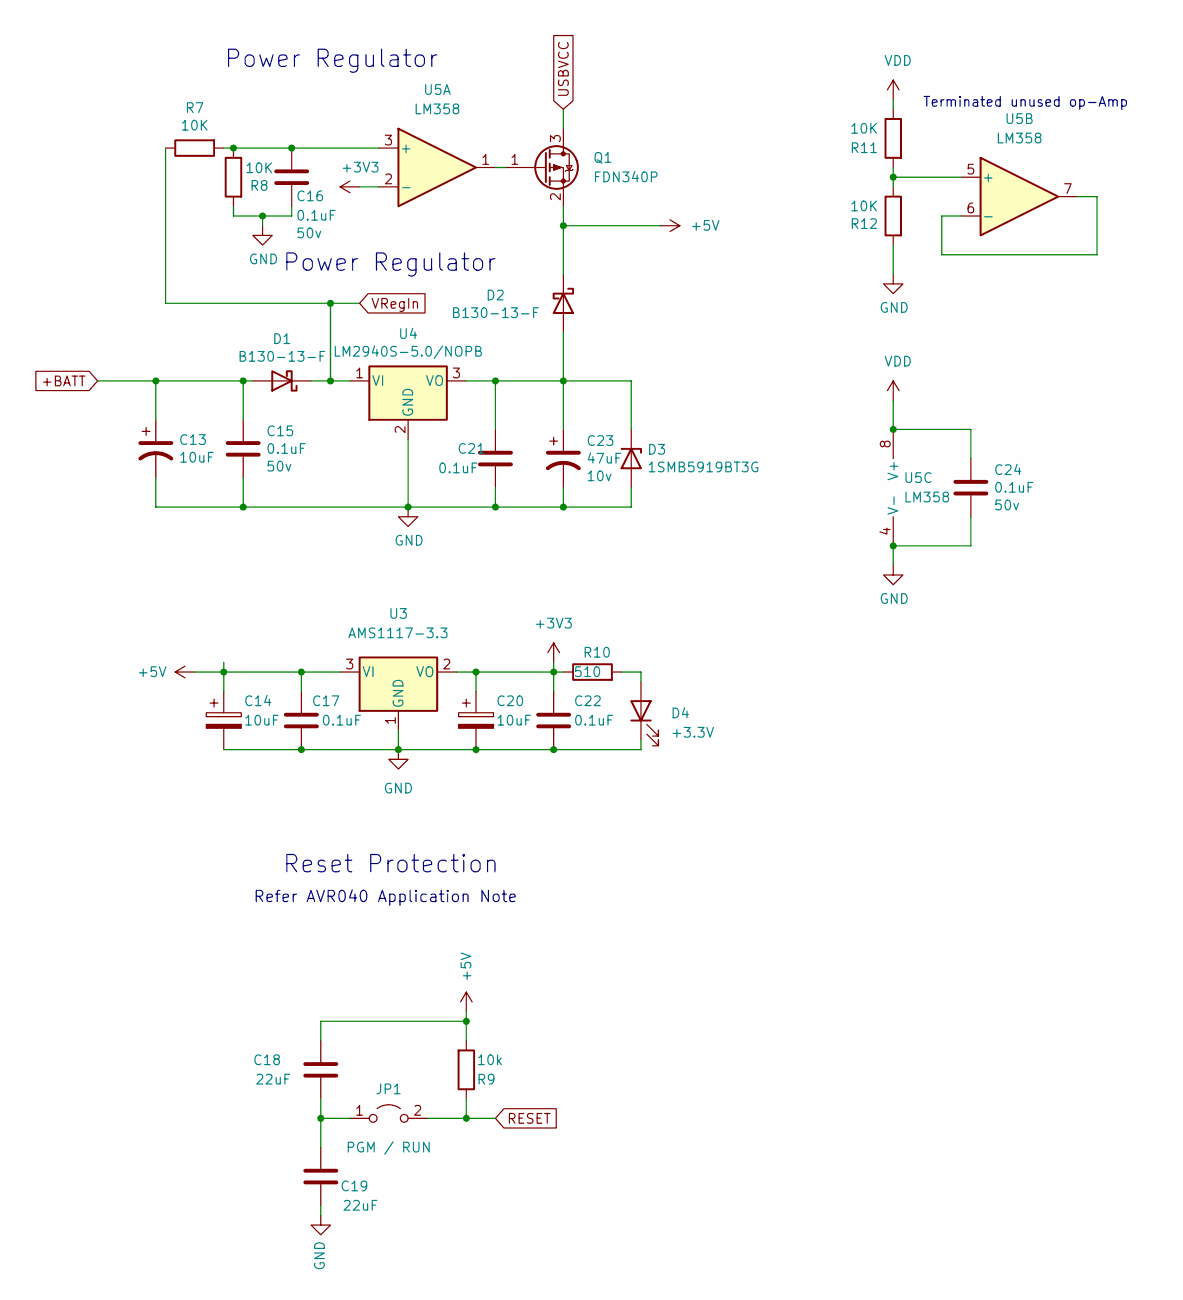
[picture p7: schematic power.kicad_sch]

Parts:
C13: 10uF; CP_EIA-7343-31_Kemet-D; Voltage 35v; LCSC Part Number C696821
C14, C20: 10uF; CP_EIA-3528-21_Kemet-B; LCSC Part Number C696821
C15, C16, C24: 0.1uF; C_0805_2012Metric; Voltage 50v; LCSC Part Number C49678
C17, C21, C22: 0.1uF; C_0805_2012Metric; LCSC Part Number C49678
C18, C19: 22uF; C_0805_2012Metric; LCSC Part Number C129303
C23: 47uF; CP_EIA-3528-21_Kemet-B; Voltage 10v
D1, D2: B130-13-F; D_SMA; LCSC Part Number C134423
D3: 1SMB5919BT3G; D_SMB; LCSC Part Number C70260
D4: +3.3V; LED_0805_2012Metric; LCSC Part Number C84256
JP1: PGM / RUN; PinHeader_1x02_P2.54mm_Vertical; LCSC Part Number C5116481
Q1: FDN340P; SOT-23; LCSC Part Number C2890122
R7, R8, R11, R12: 10K; R_0805_2012Metric; LCSC Part Number C416062
R9: 10k; R_0805_2012Metric; LCSC Part Number C416062
R10: 510; R_0805_2012Metric; LCSC Part Number C228886
U3: AMS1117-3.3; SOT-223-3_TabPin2; LCSC Part Number C2688239
U4: LM2940S-5.0/NOPB; SOT-223-3_TabPin2; LCSC Part Number C596334
U5: LM358; SOIC-8_3.9x4.9mm_P1.27mm; LCSC Part Number C16416

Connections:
+3V3: C20.1, C22.1, R10.1, U3.2 (VO), U5.2 (-)
+5V: C14.1, C17.1, C18.2, D2.1 (K), Q1.2 (S), R9.2, U3.3 (VI); also elsewhere on the board
+BATT: C13.1, C15.1, D1.2 (A); also elsewhere on the board
GND: C13.2, C14.2, C15.2, C16.2, C17.2, C19.1, C20.2, C21.2, C22.2, C23.2, C24.2, D3.2 (A), D4.1 (K), R8.2, R12.2, U3.1 (GND), U4.2 (GND), U5.4 (V-); also elsewhere on the board
unnamed: C16.1, R7.2, R8.1, U5.3 (+)
unnamed: C18.1, C19.2, JP1.1 (A)
unnamed: C21.1, C23.1, D2.2 (A), D3.1 (K), U4.3 (VO)
unnamed: D4.2 (A), R10.2
unnamed: Q1.1 (G), U5.1
unnamed: R11.2, R12.1, U5.5 (+)
unnamed: U5.6 (-), U5.7
RESET: JP1.2 (B), R9.1; also elsewhere on the board
USBVCC: Q1.3 (D); also elsewhere on the board
VDD: C24.1, R11.1, U5.8 (V+)
VRegIn: D1.1 (K), R7.1, U4.1 (VI); also elsewhere on the board

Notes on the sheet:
Power Regulator
Refer AVR040 Application Note
Reset Protection
Terminated unused op-Amp

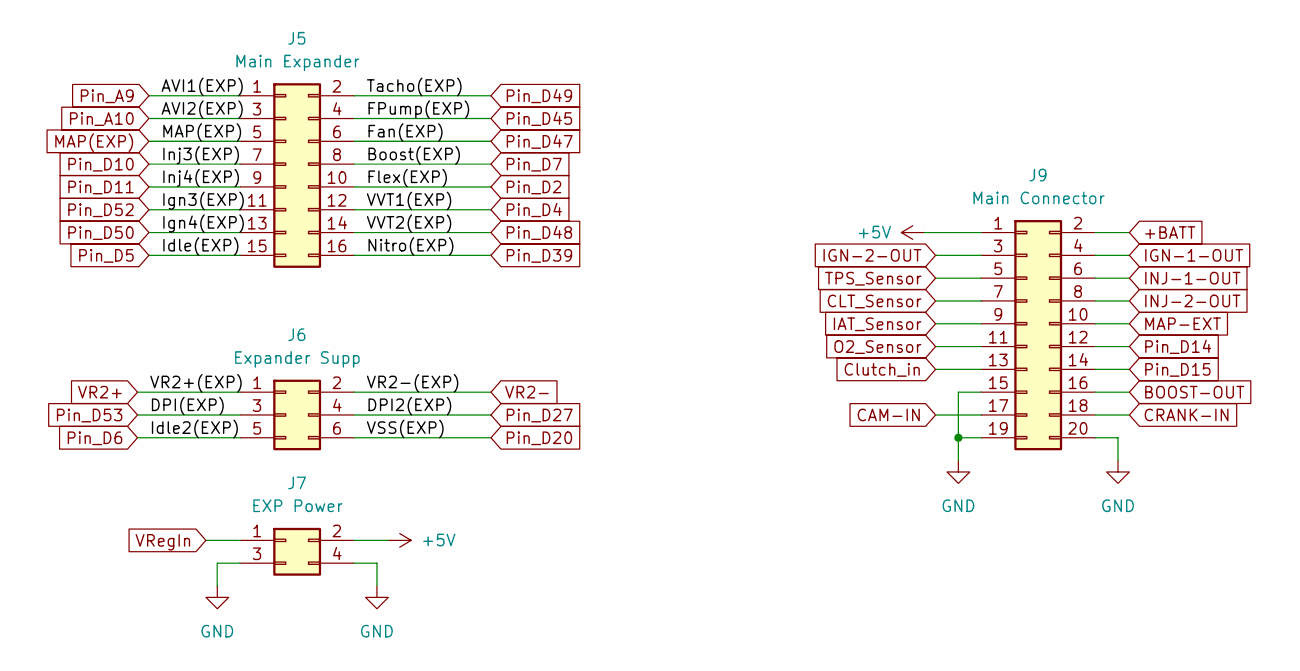
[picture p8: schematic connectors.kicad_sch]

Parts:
J5: Main Expander; Expansion 1; LCSC Part Number C917613
J6: Expander Supp; Expansion 2; LCSC Part Number C780054
J7: EXP Power; Expansion 3; LCSC Part Number C780055
J9: Main Connector; LCSC Part Number C169048

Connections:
+5V: J7.2, J9.1; also elsewhere on the board
+BATT: J9.2; also elsewhere on the board
BOOST-OUT: J9.16; also elsewhere on the board
CAM-IN: J9.17; also elsewhere on the board
CLT_Sensor: J9.7; also elsewhere on the board
CRANK-IN: J9.18; also elsewhere on the board
Clutch_in: J9.13; also elsewhere on the board
GND: J7.3, J7.4, J9.15, J9.19, J9.20; also elsewhere on the board
IAT_Sensor: J9.9; also elsewhere on the board
IGN-1-OUT: J9.4; also elsewhere on the board
IGN-2-OUT: J9.3; also elsewhere on the board
INJ-1-OUT: J9.6; also elsewhere on the board
INJ-2-OUT: J9.8; also elsewhere on the board
MAP(EXP): J5.5; also elsewhere on the board
MAP-EXT: J9.10; also elsewhere on the board
O2_Sensor: J9.11; also elsewhere on the board
Pin_A9: J5.1; also elsewhere on the board
Pin_A10: J5.3; also elsewhere on the board
Pin_D2: J5.10; also elsewhere on the board
Pin_D4: J5.12; also elsewhere on the board
Pin_D5: J5.15; also elsewhere on the board
Pin_D6: J6.5; also elsewhere on the board
Pin_D7: J5.8; also elsewhere on the board
Pin_D10: J5.7; also elsewhere on the board
Pin_D11: J5.9; also elsewhere on the board
Pin_D14: J9.12; also elsewhere on the board
Pin_D15: J9.14; also elsewhere on the board
Pin_D20: J6.6; also elsewhere on the board
Pin_D27: J6.4
Pin_D39: J5.16
Pin_D45: J5.4; also elsewhere on the board
Pin_D47: J5.6; also elsewhere on the board
Pin_D48: J5.14
Pin_D49: J5.2; also elsewhere on the board
Pin_D50: J5.13; also elsewhere on the board
Pin_D52: J5.11; also elsewhere on the board
Pin_D53: J6.3
TPS_Sensor: J9.5; also elsewhere on the board
VR2+: J6.1
VR2-: J6.2
VRegIn: J7.1; also elsewhere on the board

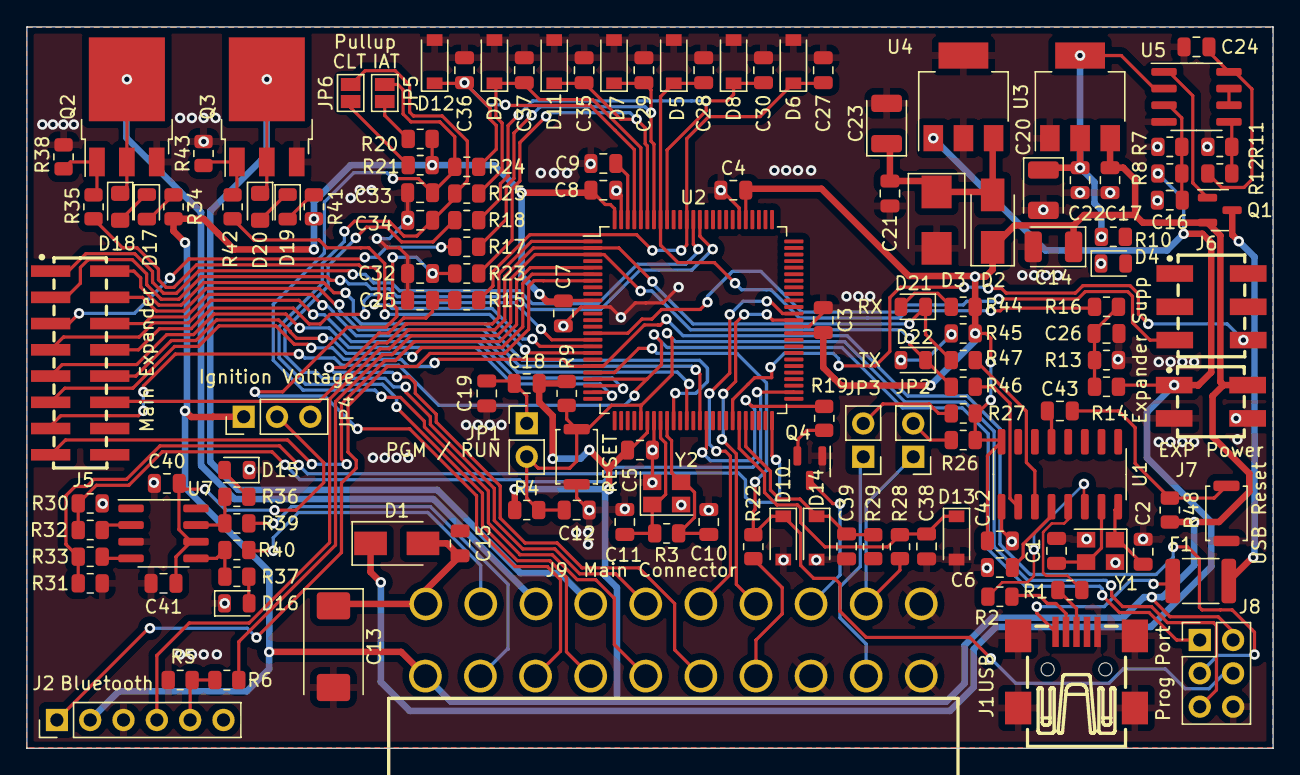
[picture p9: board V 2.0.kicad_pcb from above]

Board: 2 copper layers, 95.0 x 55.0 mm, 140 parts (0 on the bottom side), 101 nets.

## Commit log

2023-01-16 Mainboard Kicad files
    [V 2.0.kicad_pcb, V 2.0.kicad_sch, connectors.kicad_sch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]
2023-02-12 Added PDF schematics
2023-03-17 Paralela Hardware for RusEFI
    Full redesign for RusEFI compatiblity
    4x4 on board
2023-03-19 Inside a neat v1 folder
    [BOM.csv, PickAndPlace.csv]
2023-03-19 Some extra details about the board
2023-04-16 Attacked all present issues
    -add "alive" blue LED that is activated once firmware is properly loaded
    ADDED BLUE COMMS LED
    -use lower intensity LEDs for 5v and 12v
    ADDED HIGHER RESISTORS, TO LIMIT THE CURRENT TO 1MA, WHICH SHOULD BRING
    DOWN THE INTENSITY / BRIGHTNESS.
    -add diode on top layer for MCU power over USB
    DIODE REMOVED FROM THE BOTTOM, PLACED ON THE TOP LAYER
    -add GND and 3.3v pins for programming, maybe remove NRST as it is not required
    ADDED 6 PIN, PIN CONNECTOR TO ADD 5V, 3V3, GND, NRST, ST-CLK, ST-DIO
    [BOM.csv, PickAndPlace.csv]
2023-09-19 V2 with fuel pump output fix
    Fuel pump did not work right, now fixed
    [BOM - Copy.csv, BOM.csv, PickAndPlace.csv]
